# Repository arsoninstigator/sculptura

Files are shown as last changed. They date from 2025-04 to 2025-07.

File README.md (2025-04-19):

# sculptura ☆.ᐟ

## about
sculptura is a fully **open-source** work-in-progress and customized budget corexy 3d printer that was made for hack club's #infill program <br>



## building
<b>aim -</b> an easy-to-assemble printer for printing smooth, detailed and precise models. handling aesthetic blends of filled/textured filaments at ease, making prints that are meant to to be used as high quality decorative pieces (like you would see at an art gallery). aka a printer designed for crisp details and clean surface textures, not industrial tolerances.

## features
- corexy incorporating a p1p-style z-axis
- build volume: 200×200×200 mm
- up to 300°C hotend temperature
- dedicated part cooling (5015 blower) & always-on hotend cooling (4010 fan)
- built for klipper firmware
- fits in the 500 USD budget & uses 150 USD of my own funds
- hackable and easy to remix: change build volume, components, mounts, etc.
- enclosable design for stable print environment + designed for easy assembly
- fully parametric cad design - [see here](https://a360.co/4czRthb)

## final results
sculptura's direct drive, high-temp hotend setup makes it great for fun filaments:
- wood pla
- marble pla
- silk pla
- glow-in-the-dark pla
- other aesthetic blends
- matte/fiber-filled filaments (pla, petg, etc.) <br>

it allows reliable extrusion of filaments without clogging or excessive stringing. plus with input shaping and linear rails, the printer minimizes ghosting and ringing resulting in cleaner ripple-free detailing and polished finishes.

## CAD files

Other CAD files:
sculptura.step

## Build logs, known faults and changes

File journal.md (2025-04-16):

# sculptura ☆.ᐟ

> username: @arsoninstigator aka @anne on the slack (she/her) <br>
> here's the printer's [github repository](https://arsoninstigator/sculptura) and the main [infill page](https://infill.hackclub.com/printers/sculptura/) <br>
> total time spent on this till date: 81 hours
- [X] i currently / will have access to a 3d printer before 21st march (bambu a1 mini)

## about
sculptura is a fully **open-source** and customized budget corexy 3d printer  that incorporates a p1p-style z-axis and was made for hack club's #infill <br>
> <b>my initial aim -</b> for printing smooth, detailed and precise models with aesthetic blends of filled/textured filaments that are meant to to be used as high quality decorative pieces (like you would see at an art gallery) :D



## daily log
### ⋆ day one - day ten — initial research (time taken: ~ 15h)
found out even more about how 3d printers work by reading documents, watching youtube videos, looking at existing open-source builds (including neutrino), sketching out what i was trying to achieve. i loosely consulted reddit threads that answered my super specific questions and asked a lot of questions on dedicated discord servers (i'm surprised they didn't ban me for being annoying). i did my initial light research on:
- frame and motion system
  - frame design & materials
  - printer kinematics & motion types
  - linear motion
  - belt & pulley system
- extruder and hotend
  [i spent a lot of time going back and forth to decide whether i wanted to make a clay or paste-y printer (since the name of my printer is sculptura) but ultimately decided against it and took the traditional route]
  - hotend types
  - nozzles & material compatibility
  - direct drive
- bed and print surface
- firmware (will run klipper)
- electronics
  - mainboard selection
  - stepper motor drivers
  - power supply & wiring

at this point i obviously knew only the basics so nothing was set in stone but i started to form a **very rough image** in my head of what my printer would look like and started to make interations on the components i had chosen and added to my current bom before i started cad-ding and got in too deep!

### ⋆ day eleven - day nineteen — research + begin cad (time taken: ~ 17h)
continued my quest to research on more stuff and get into the details. watched actual people talk about their experience working w 3d printer builds to get a holistic view that's beyond the pages of a book. some topics i covered included:
- bed & print surface
  - heated bed types
  - bed surfaces
  - auto bed leveling?
- cooling & enclosure design
  - part cooling fans and ducts
  - hotend cooling fans
  - enclosures and filtration

sketched out a wip printer and its measurements with a paper/pencil and then started working on the cad. focused on the frame. decided: aluminum extrusions, no question. modeled a simple 2020 extrusion profile, then tried to boolean it into a frame mockup. fusion crashed twice. used a combination of fusion 360 and freecad (love the open source-ness but it's not quite there yet in terms of features) and even though this wasn't the hardest part of the build, but i had to restart from scratch multiple times and do it all over again and again till i was somewhat satisfied with the results.

### ⋆ day twenty - day twenty-five — cadding
realized i didn’t dimension the extrusion lengths. spent a whole day fixing it. fusion's sketch constraints started ghosting me. drove myself mad figuring out why my midpoint constraint wasn’t snapping. next day, found a nice trick on grabcad for corner brackets. "borrowed" the design and parameterized it to fit my frame. made fusion crash only once which is a victory in itself in my book. next two days, scrolled discord printer groups. stumbled across some fun idler designs. screenshot folder became 134 images deep. did no cad stuff since i felt kinda burnt out. after that, finally locked in and started laying out core xy belt paths. sketched some pulleys and tried routing the belt. decided it looked like spaghetti and got hungry. googled “corexy belt routing diagram” 17 times and was still confused.

### ⋆ day twenty six - day thirty two
made some core xy progress - refined the belt paths. added idler pulley placeholders. felt like a god for 30 minutes until i realized i forgot to check belt tensioning. next day, modeled my first tensioner block. completely forgot clearance for the screw head. redid the whole thing. scrapped it entirely in anger. redid it *again*. next, i borrowed some gantry ideas from voron. decided on linear rails. modeled a rail and slapped it onto the frame. *wingardium laviosa* noticed it's floating in mid-air but oh well. next, added actual mounting points to the frame for rails. realized i sized them 3mm too short. adjusted everything. fusion performance starting to tank from component count. next, modeled a rough carriage and constrained it to slide on the x rail. watching it move felt great. next, added pulley mounts to the carriage. spent 40 minutes debating between single or dual pulleys. settled on dual for tensioning flexibility. upped my dosage for ritalin (prescribed ofc) to lock in but fell asleep with fusion open and my head on the keyboard so that went as well as you can imagine.

### ⋆ day thirty-three - day forty
designed a motor mount plate. fusion crashed during patterning. auto-recovered my file but lost constraints. raged. cried. ate chips. returned. next day, ranted in my journal about fusion not autosaving often enough. redesigned motor mount properly this time. frame finally started feeling real !!! next, got stuck deciding between optical or mechanical endstops. prototyped a slot for microswitches, decided to stay simple. will probably regret this later. next, modeling the y carriages today. realized they look suspiciously like voron’s. decided that was good ??? looked up juvenile sentences for shoplifting (/s). next, redesigned how extrusions join for better rigidity. added hidden fasteners. model was getting heavy but fusion was surprisingly cooperative. next, discovered i need spacers everywhere. modeled one spacer, then made 12 variants. started going insane and had to go for a walk. started raining while i was walking. yay. 

### ⋆ day forty-one - day forty-five — printhead-ing + electronics
explored printhead designs. half-considered a compact, single-fan setup but ended up copying a stealthburner clone layout. next, modeled the printhead mount. forgot to add wire management. amazing. next, finally added wire guides. fusion assemblies slowed to 5 fps but the model looked neat. next, roughed out a bottom electronics compartment. stole layout inspiration from voron switchwire. power supply mount looked questionable. felt pointless spending an hour designing a snazzy power button mount. next, added cutouts for ac inlet and exhaust fan. the model had started looking suspiciously printer-like.

### ⋆ day forty-six onwards — wrapping up the printer
modeled some custom fan grills. made them a bit too decorative. questioned my aesthetic priorities. next, started mocking up bed mounting. spring setup first, decided that i will explore silicone mounts later. next, modeled bed leveling knobs. realized i hate knobs. felt like i might switch to automatic probing. took a break from the printer to model a cookie cutter for fun (and #bakebuild). next, modeled a mount for a bed probe. debating between bltouch or inductive sensor. prototyped both. decided that it looked slick. next, added fasteners to most major components. took some vanity renders of the assembly. cursed the bloodline of whoever created fusion. next, spent an unhealthy amount of time designing a filament guide path. cleaned up the toolhead design. was actually happy with this iteration. next, fusion constraints exploded mysteriously. spent 3 hours untangling dependencies. next, modeled a simple filament runout sensor holder. used a borrowed sensor design. printer started looking somehwat complete. chamfered edges, added fillets, prettied up exposed mounts because #vibes. revisited motor mounts. strengthened weak points. added bed cable chain mount. model complexity was at an all-time high. did some fancy renders again. asked mom for color palette inspiration since my model looked ... sad.
<br> <br>
designed enclosure panels for my printer (the 20$ printer mod mini ysws) which finally looked like a printer. 

### ⋆ present
worked on the readme/journal log for my printer :3 made a list of future modifications i would like to make (when i have time + extra funding of my own). worked on the bill of materials which was a pain because hcb cards dont always work in india + aliexpress etc. and other chinese manufacturers are simply banned in india + so it was a hit or miss + the tariffs now made everything so much harder to source because hobby electronics in india is not cheap. at all. 

## final results
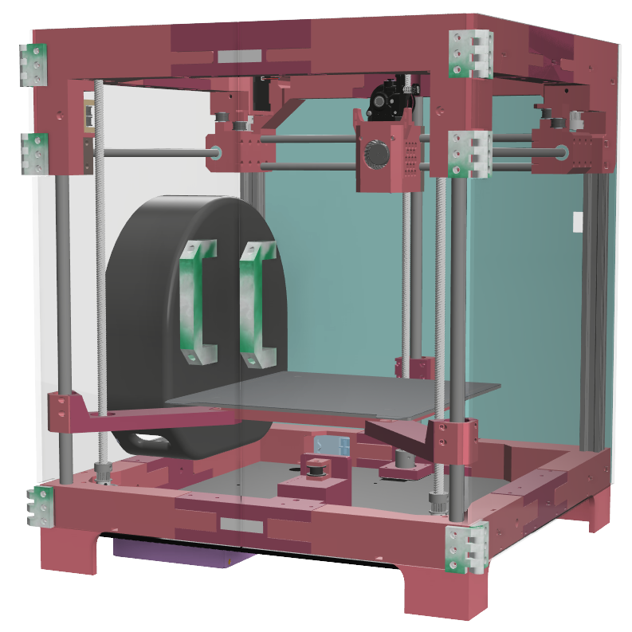
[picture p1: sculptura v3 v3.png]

cad link - [here](https://a360.co/4czRthb)
<br><br>
sculptura's direct drive, high-temp hotend setup makes it great for fun filaments:
- wood pla
- marble pla
- silk pla
- glow-in-the-dark pla
- other aesthetic blends
- matte/fiber-filled filaments (pla, petg, etc.) <br>

it allows reliable extrusion of filaments without clogging or excessive stringing. plus also with klipper firmware and input shaping, the printer minimizes ghosting and ringing resulting in cleaner detailing and polished finishes.

note that this is only the case if you:
- use a hardened steel or ruby-tipped nozzle (the fillers can wear out brass nozzles fast)
- don’t clog the hotend (wood pla especially is a pain if you print too hot / slow)

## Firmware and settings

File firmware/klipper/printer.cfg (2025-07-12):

[include mainsail.cfg]
[include pinout_aliases.cfg]
[include mks_mini_12864_v3.cfg]
[exclude_object]
#[include adxl.cfg]

[printer]
kinematics: corexy
max_velocity: 600
max_accel: 7500 # change this to 7500 after commissioning
max_z_velocity: 3   # may be able to increase to 15 after comissioning.
max_z_accel: 50
square_corner_velocity: 5 # start at 8, but then increase once you're sure assembly is sound

[mcu] 
serial: /dev/serial/by-id/usb-Klipper_stm32f407xx_350050001251323439393937-if00


[gcode_macro CALIBRATE_BED_LEVEL]
gcode:
  G28
   BED_MESH_CALIBRATE

[gcode_macro PRINT_START]
#   Use PRINT_START for the slicer starting script - PLEASE CUSTOMISE THE SCRIPT
gcode:       
    CALIBRATE_BED_LEVEL

## Wipe Macro####


# Stepper Configs
[stepper_x]
# connected to X Stepper
step_pin: PC14
dir_pin: !PC13
enable_pin: !PC15
rotation_distance: 40
full_steps_per_rotation: 200
microsteps: 32
endstop_pin: tmc2209_stepper_x:virtual_endstop 
position_endstop: 243
position_min: 0
position_max: 260
homing_speed: 100
homing_retract_dist: 0

[tmc2209 stepper_x]
# connected to X Stepper
uart_pin: PE6
run_current: 0.9 #was .9
sense_resistor: 0.110
#stealthchop_threshold: 999999
interpolate: False #was false
diag_pin: PA14
driver_SGTHRS: 170

[stepper_y]
# connected to Y Stepper
step_pin: PE5
dir_pin: PE4
enable_pin: !PC15
rotation_distance: 40
full_steps_per_rotation: 200
microsteps: 32
endstop_pin: tmc2209_stepper_y:virtual_endstop
position_endstop: 230
position_max: 230
homing_speed: 100
homing_retract_dist: 0

[tmc2209 stepper_y]
# connected to Y Stepper
uart_pin: PE3
run_current: 0.9 #was .9
sense_resistor: 0.110
#stealthchop_threshold: 999999
interpolate: False #was false
diag_pin: PA15 
driver_SGTHRS: 170

[stepper_z]
step_pin: PE1
dir_pin: PE0
enable_pin: !PE2
rotation_distance: 2
full_steps_per_rotation: 200
microsteps: 32
endstop_pin: probe:z_virtual_endstop
position_min: -10
position_max: 150
homing_speed: 100
homing_retract_dist: 10


[tmc2209 stepper_z]
# connected to Z Stepper
uart_pin: PB7
run_current: 0.9
sense_resistor: 0.110
#stealthchop_threshold: 999999
interpolate: False #was false
diag_pin: PB13



# Extruder0
[extruder]
# connected to E4 Stepper
step_pin: PD13
dir_pin: !PD12
enable_pin: !PB6
rotation_distance: 4.4637
microsteps: 16
full_steps_per_rotation: 200
nozzle_diameter: 0.400
pressure_advance: 0.03
pressure_advance_smooth_time: 0.040
filament_diameter: 1.750	

# connected to TH0
sensor_type: ATC Semitec 104GT-2
sensor_pin: PC1

min_extrude_temp: 0
min_temp: -200
max_temp: 999
# connected to HE0
heater_pin: PB1
max_power: 1.0
max_extrude_only_distance: 1400.0
max_extrude_only_velocity: 120.0
max_extrude_only_accel: 1500.0
max_extrude_cross_section: 20000.0

[tmc2209 extruder]
# connected to E4 Stepper
uart_pin: PD11
run_current: 0.4
sense_resistor: 0.110
#stealthchop_threshold: 0
interpolate: False


# connected to Heater0
# Fans  
# Hotend Cooling Fan
[heater_fan my_nozzle_fan]
# connected to Fan0 - 24v Fan
pin: PA2
max_power: 1.0
#kick_start_time: 0.5
heater: extruder
heater_temp: 50.0
 
# print cooling fan
[fan]
# connected to Fan1 - 12v Fan
pin: PA0
max_power: 1.0
kick_start_time: 0.500



[heater_bed]
heater_pin: PB10
sensor_type: Generic 3950
sensor_pin: PC0
max_power: 1.0
min_temp: 0
max_temp: 120

[input_shaper]
shaper_freq_x: 0
shaper_freq_y: 0
shaper_type: mzv

[probe]
#Z_offset: 0.0
pin: PA8


[bed_mesh]
speed: 60
horizontal_move_z: 5

mesh_min: 20, 35
mesh_max: 200, 220
probe_count: 4, 4

[safe_z_home]
home_xy_position: 115, 115 # Change coordinates to the center of your print bed
speed: 50
z_hop: 0                 # Move up 10mm
z_hop_speed: 5


#Gcode G2/G3 Arc Support
[gcode_arcs]
resolution: 0.1

# Motor and Heater Idle Timeout
[idle_timeout]
timeout: 6000

[respond]

#*# <---------------------- SAVE_CONFIG ---------------------->
#*# DO NOT EDIT THIS BLOCK OR BELOW. The contents are auto-generated.
#*#
#*# [extruder]
#*# control = pid
#*# pid_kp = 43.538
#*# pid_ki = 16.125
#*# pid_kd = 29.388
#*#
#*# [bed_mesh default]
#*# version = 1
#*# points =
#*# 	0.301250, 0.803750, 0.634062, 0.632500
#*# 	-0.014375, 0.453125, 0.445625, 0.445000
#*# 	-0.520938, 0.086250, 0.057187, 0.155937
#*# 	-1.665938, -0.863125, -0.592500, -0.581250
#*# x_count = 4
#*# y_count = 4
#*# mesh_x_pps = 2
#*# mesh_y_pps = 2
#*# algo = lagrange
#*# tension = 0.2
#*# min_x = 20.0
#*# max_x = 200.0
#*# min_y = 35.0
#*# max_y = 219.98
#*#
#*# [heater_bed]
#*# control = pid
#*# pid_kp = 70.188
#*# pid_ki = 1.248
#*# pid_kd = 987.021
#*#
#*# [probe]
#*# z_offset = 0.885
